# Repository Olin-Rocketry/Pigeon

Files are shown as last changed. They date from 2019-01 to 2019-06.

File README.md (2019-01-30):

# Pigeon
simple flight computer to serve as a learning bed for embedded software and pcb design.

## Features
- atmega328p-AU
- battery connector (JST-PH 2-pin)
- 3-axis accelerometer (ADXL345)
- 2 or 3 programming leds
- SD-Card reader
-level stepper for SD-Card

## Requirements
- fit in our current rocket (same dimensions as peregrine)
- run time greater than 30 minutes

## Goals
- learning platform for incoming members
- test/optimize SD-Card write performance

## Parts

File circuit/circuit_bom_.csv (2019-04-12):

Component | Description | Part | References | Value | Footprint | Quantity Per PCB | Datasheet | MFN | MPN | PurchasingLink | Purchasing Link | Digi-Key Part Number
1 | b'' | b'C_0.1uF' | b'C2' | b'C_0.1uF' | b'C_0805_OEM' | b'1' | b'http://datasheets.avx.com/X7RDielectric.pdf' | b'DK' | b'478-3352-1-ND' | b'https://www.digikey.com/products/en?keywords=478-3352-1-ND' | b'' | b''
2 | b'' | b'C_0.1uF' | b'C7' | b'C_0.1uF' | b'C_0805_OEM' | b'1' | b'http://datasheets.avx.com/X7RDielectric.pdf' | b'DK' | b'478-3352-1-ND' | b'https://www.digikey.com/products/en?keywords=478-3352-1-ND' | b'' | b''
3 | b'' | b'C_0.1uF' | b'C9' | b'C_0.1uF' | b'C_0805_OEM' | b'1' | b'http://datasheets.avx.com/X7RDielectric.pdf' | b'DK' | b'478-3352-1-ND' | b'https://www.digikey.com/products/en?keywords=478-3352-1-ND' | b'' | b''
4 | b'' | b'C_100pF' | b'C6' | b'C_100pF' | b'C_0805_OEM' | b'1' | b'https://katalog.we-online.de/pbs/datasheet/885012007057.pdf' | b'DK' | b'732-7852-1-ND' | b'https://www.digikey.com/product-detail/en/wurth-electronics-inc/885012007057/732-7852-1-ND/5454479' | b'' | b''
5 | b'' | b'C_1uF' | b'C1' | b'C_1uF' | b'C_0805_OEM' | b'1' | b'http://www.samsungsem.com/kr/support/product-search/mlcc/__icsFiles/afieldfile/2018/06/20/CL21A105KAFNNNE.pdf' | b'DK' | b'1276-2887-1-ND' | b'https://www.digikey.com/product-detail/en/samsung-electro-mechanics/CL21A105KAFNNNE/1276-2887-1-ND/3890973' | b'' | b''
6 | b'' | b'C_1uF' | b'C3' | b'C_1uF' | b'C_0805_OEM' | b'1' | b'http://www.samsungsem.com/kr/support/product-search/mlcc/__icsFiles/afieldfile/2018/06/20/CL21A105KAFNNNE.pdf' | b'DK' | b'1276-2887-1-ND' | b'https://www.digikey.com/product-detail/en/samsung-electro-mechanics/CL21A105KAFNNNE/1276-2887-1-ND/3890973' | b'' | b''
7 | b'' | b'C_1uF' | b'C8' | b'C_1uF' | b'C_0805_OEM' | b'1' | b'http://www.samsungsem.com/kr/support/product-search/mlcc/__icsFiles/afieldfile/2018/06/20/CL21A105KAFNNNE.pdf' | b'DK' | b'1276-2887-1-ND' | b'https://www.digikey.com/product-detail/en/samsung-electro-mechanics/CL21A105KAFNNNE/1276-2887-1-ND/3890973' | b'' | b''
8 | b'' | b'C_30pF' | b'C4 C5' | b'C_30pF' | b'C_0805_OEM' | b'2' | b'https://media.digikey.com/pdf/Data%20Sheets/Samsung%20PDFs/CL_Series_MLCC_ds.pdf' | b'DK' | b'1276-1130-1-ND' | b'https://www.digikey.com/product-detail/en/samsung-electro-mechanics-america-inc/CL21C300JBANNNC/1276-1130-1-ND/3889216' | b'' | b''
9 | b'' | b'LED_0805' | b'D1 D2 D3' | b'LED_0805' | b'LED_0805_OEM' | b'3' | b'http://www.osram-os.com/Graphics/XPic9/00078860_0.pdf' | b'DK' | b'475-1410-1-ND' | b'https://www.digikey.com/products/en?keywords=475-1410-1-ND' | b'' | b''
10 | b'' | b'JST-PH_2_RA' | b'J1' | b'JST-PH_2_RA' | b'JST-PH_2_RA' | b'1' | b'https://cdn-shop.adafruit.com/datasheets/17311.pdf' | b'' | b'' | b'' | b'https://www.adafruit.com/product/1769' | b''
11 | b'' | b'R_100' | b'R7' | b'R_100' | b'R_0805_OEM' | b'1' | b'https://www.seielect.com/Catalog/SEI-rncp.pdf' | b'DK' | b'RNCP0805FTD100RCT-ND' | b'https://www.digikey.com/products/en?keywords=RNCP0805FTD100RCT-ND' | b'' | b''
12 | b'' | b'R_10K' | b'R9 R11' | b'R_10K' | b'R_0805_OEM' | b'2' | b'http://www.bourns.com/data/global/pdfs/CRS.pdf' | b'DK' | b'CRS0805-FX-1002ELFCT-ND' | b'https://www.digikey.com/products/en?keywords=CRS0805-FX-1002ELFCT-ND' | b'' | b''
13 | b'' | b'R_10K' | b'R4 R6' | b'R_10K' | b'R_0805_OEM' | b'2' | b'http://www.bourns.com/data/global/pdfs/CRS.pdf' | b'DK' | b'CRS0805-FX-1002ELFCT-ND' | b'https://www.digikey.com/products/en?keywords=CRS0805-FX-1002ELFCT-ND' | b'' | b''
14 | b'' | b'R_200' | b'R1 R2 R3 R5' | b'R_200' | b'R_0805_OEM' | b'4' | b'https://www.seielect.com/Catalog/SEI-RMCF_RMCP.pdf' | b'DK' | b'RMCF0805JT200RCT-ND' | b'https://www.digikey.com/products/en?keywords=RMCF0805JT200RCT-ND' | b'' | b''
15 | b'' | b'R_4.7K' | b'R8 R10' | b'R_4.7K' | b'R_0805_OEM' | b'2' | b'http://www.yageo.com/documents/recent/PYu-RC_Group_51_RoHS_L_8.pdf' | b'DK' | b'311-4.7KARCT-ND' | b'https://www.digikey.com/product-detail/en/yageo/RC0805JR-074K7L/311-4.7KARCT-ND/731274' | b'' | b''
16 | b'' | b'Micro_SD_Card_A118117CT-ND' | b'SD1' | b'Micro_SD_Card_A118117CT-ND' | b'Micro_SD_Card_A118117CT-ND' | b'1' | b'https://www.te.com/commerce/DocumentDelivery/DDEController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' | b'' | b'2201778-1' | b'' | b'' | b'A118117CT-ND'
17 | b'' | b'4050_Logic_Buffer' | b'U6' | b'4050_Logic_Buffer' | b'SOIC-16_3.9x9.9mm_Pitch1.27mm' | b'1' | b'www.ti.com/lit/ds/symlink/cd74hc4049.pdf' | b'' | b'' | b'' | b'https://www.digikey.com/product-detail/en/texas-instruments/CD74HC4050M96/296-14529-1-ND/555596' | b''
18 | b'' | b'ADXL345' | b'U3' | b'ADXL345' | b'ADXL345' | b'1' | b'http://www.analog.com/media/en/technical-documentation/data-sheets/ADXL345.pdf' | b'DK' | b'ADXL345BCCZ-ND' | b'https://www.digikey.com/product-detail/en/analog-devices-inc/ADXL345BCCZ/ADXL345BCCZ-ND/2034829' | b'' | b''
19 | b'20MHz, 32kB Flash, 2kB SRAM, 1kB EEPROM, TQFP-32' | b'ATmega328-AU' | b'U4' | b'ATmega328-AU' | b'TQFP-32_7x7mm_Pitch0.8mm' | b'1' | b'http://ww1.microchip.com/downloads/en/DeviceDoc/ATmega328_P%20AVR%20MCU%20with%20picoPower%20Technology%20Data%20Sheet%2040001984A.pdf' | b'' | b'' | b'' | b'' | b''
20 | b'' | b'SK812' | b'U1' | b'SK812' | b'SK6812' | b'1' | b'https://cdn-shop.adafruit.com/product-files/1138/SK6812+LED+datasheet+.pdf' | b'' | b'' | b'https://www.digikey.com/product-detail/en/adafruit-industries-llc/1655/1528-1104-ND/5154679' | b'' | b''
21 | b'' | b'TCR2EF33LM' | b'U2' | b'TCR2EF33LM' | b'SOT25' | b'1' | b'https://toshiba.semicon-storage.com/info/docget.jsp?did=13794&prodName=TCR2EF45' | b'' | b'TCR2EF33LM(CTCT-ND' | b'' | b'https://www.digikey.com/product-detail/en/toshiba-semiconductor-and-storage/TCR2EF33LM-CT/TCR2EF33LM-CTCT-ND/4503328' | b''
22 | b'' | b'USB_MicroB' | b'U5' | b'USB_MicroB' | b'USB_Micro-B_Molex-105017-0001' | b'1' | b'https://www.molex.com/pdm_docs/sd/1050170001_sd.pdf' | b'DK' | b'WM1399CT-ND' | b'https://www.digikey.com/product-detail/en/molex-llc/1050170001/WM1399CT-ND/2350885' | b'' | b''
23 | b'' | b'Crystal_SMD' | b'Y1' | b'Crystal_SMD' | b'Crystal_SMD_FA238' | b'1' | b'https://support.epson.biz/td/api/doc_check.php?dl=brief_FA-238V_en.pdf' | b'DK' | b'SER3686CT-ND' | b'https://www.digikey.com/products/en?keywords=SER3686CT-ND' | b'' | b''
Component Groups: | 23
Component Count: | 32
Fitted Components: | 32
Number of PCBs: | 1
Total components: | 32
Schematic Version:
Schematic Date:
BoM Date: | b'Tue 02 Apr 2019 08:23:06 PM EDT'
Schematic Source: | b'/home/william/Desktop/pigeon/circuit/circuit.sch'
KiCad Version: | b'Eeschema 5.0.0-fee4fd1~66~ubuntu16.04.1'

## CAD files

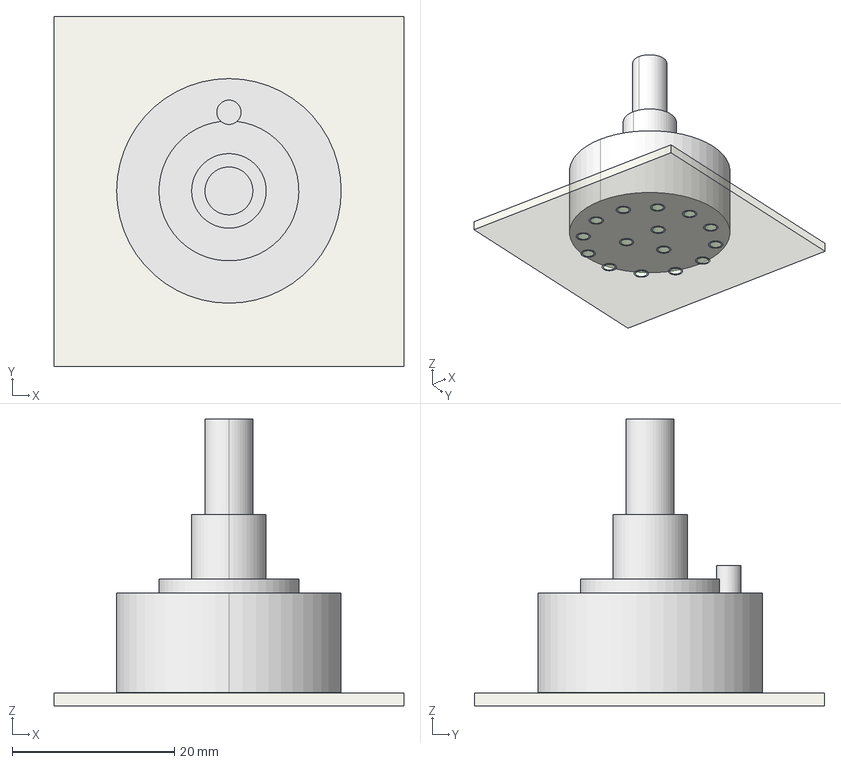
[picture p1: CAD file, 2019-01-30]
3DModels/3P4T_rotary_switch/3P4T_rotary_switch.fcstd
43.2 x 43.2 x 35.4 mm
FrontSilk
TopPads
BotPads
PTHs
Pcb
prog_switch

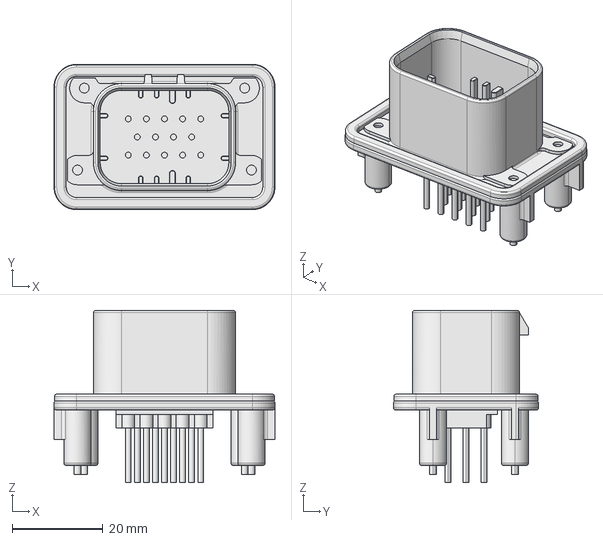
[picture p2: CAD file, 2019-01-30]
3DModels/Ampseal-14/AmpSeal-14.step
48.8 x 32.1 x 38.1 mm

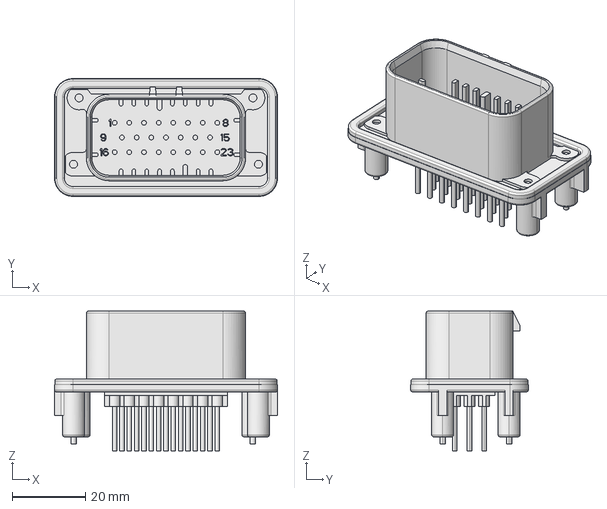
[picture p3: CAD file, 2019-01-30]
3DModels/Ampseal-23/Ampseal_23.step
60.8 x 32.1 x 38.1 mm

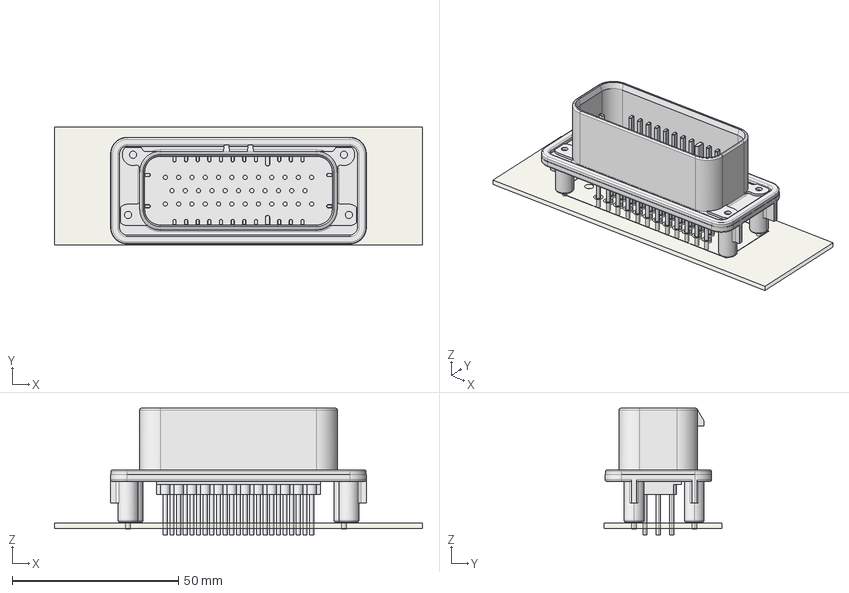
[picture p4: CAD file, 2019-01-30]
3DModels/Ampseal-35/Ampseal-35.fcstd
110.6 x 35.4 x 38.0 mm
FrontSilk
TopPads
BotPads
PTHs
Pcb
C-1-776231-4

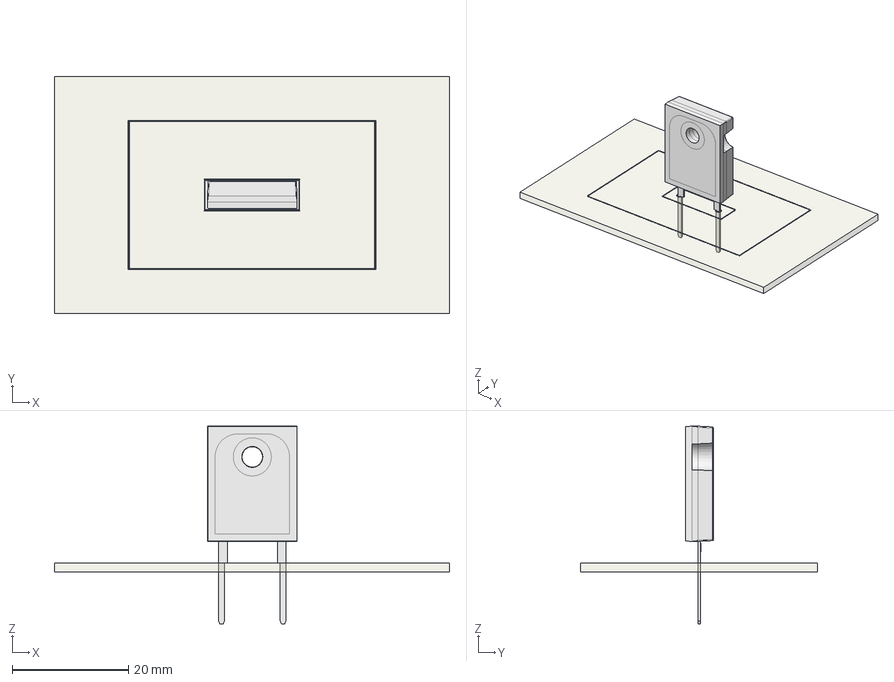
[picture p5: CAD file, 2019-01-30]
3DModels/AP101_3k_resistor/AP101.fcstd
68.0 x 40.8 x 34.0 mm
F_CrtYd
FrontSilk
TopPads
BotPads
PTHs
Pcb
TIP 144_sp

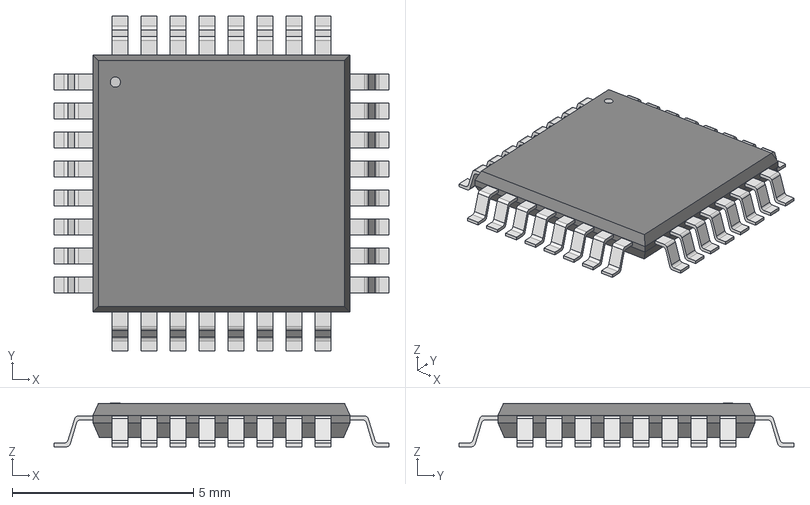
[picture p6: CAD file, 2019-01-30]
3DModels/Atmega16m1/32A-M.step
9.25 x 9.25 x 1.20 mm

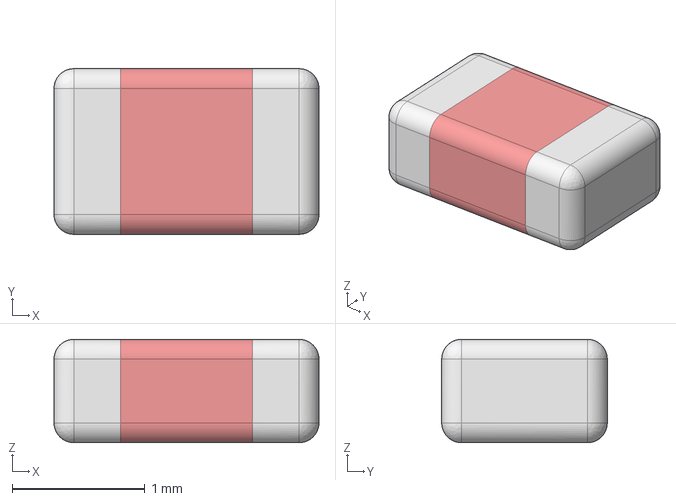
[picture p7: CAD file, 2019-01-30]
3DModels/C_0805_OEM/C_0805.step
2.00 x 1.25 x 0.78 mm

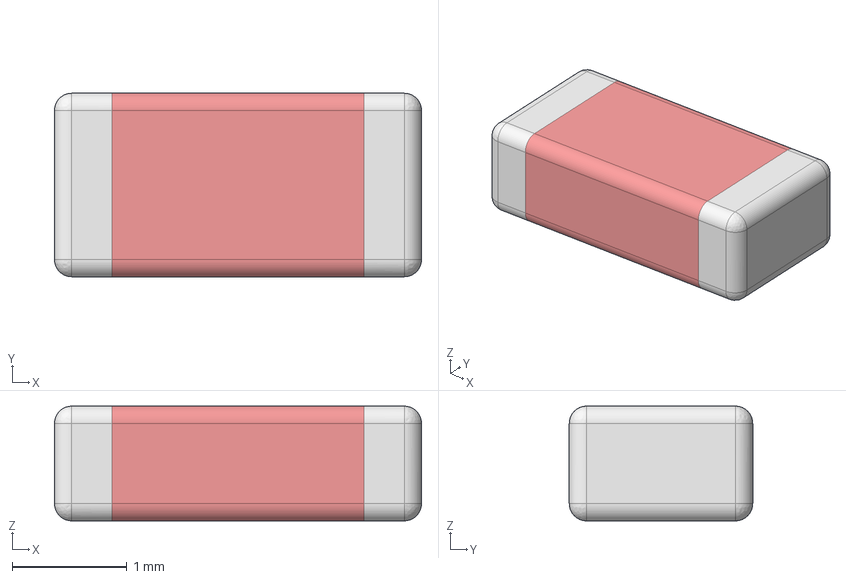
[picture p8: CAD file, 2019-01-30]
3DModels/C_1206_OEM/C_1206_OEM.step
3.20 x 1.60 x 1.00 mm

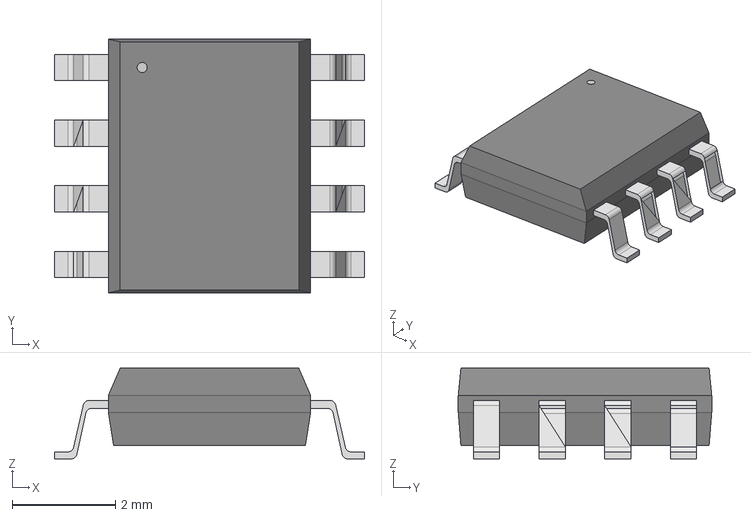
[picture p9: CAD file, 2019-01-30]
3DModels/CAN Transceiver/CAN Transceiver.step
5.99 x 4.90 x 1.75 mm

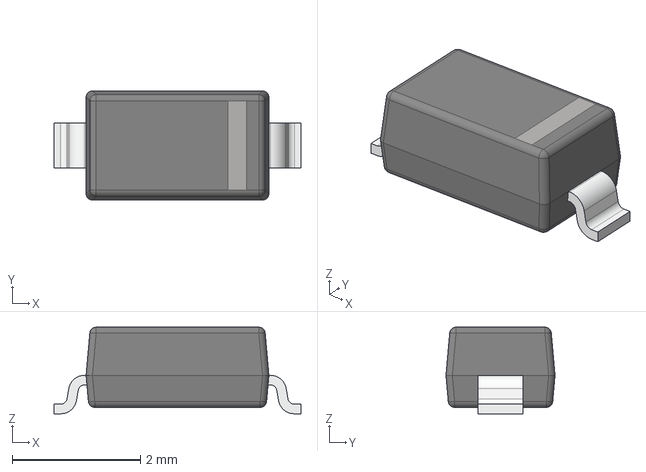
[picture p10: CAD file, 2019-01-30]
3DModels/D_Schottky_SOD123/DO-215AD002_sp.step
3.85 x 1.70 x 1.35 mm

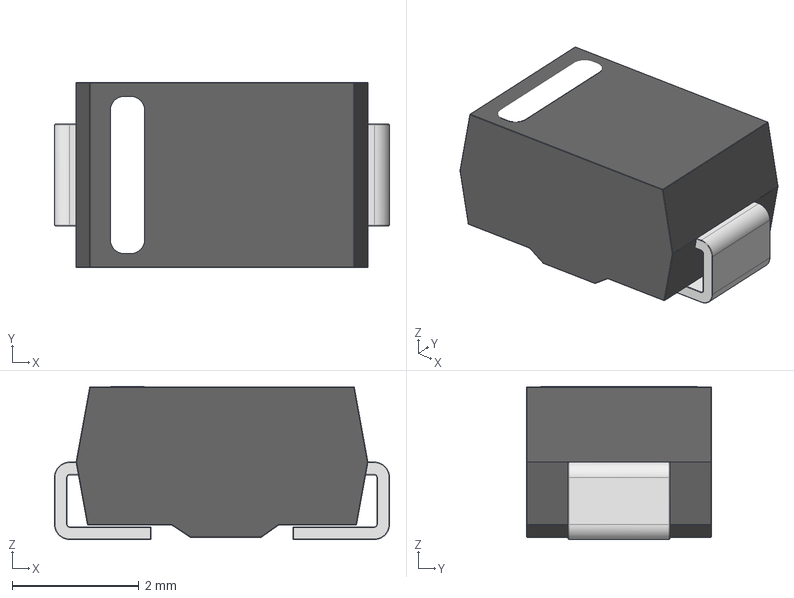
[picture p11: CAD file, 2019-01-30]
3DModels/DO_214AA_OEM/DO_214AA.step
5.28 x 2.92 x 2.41 mm

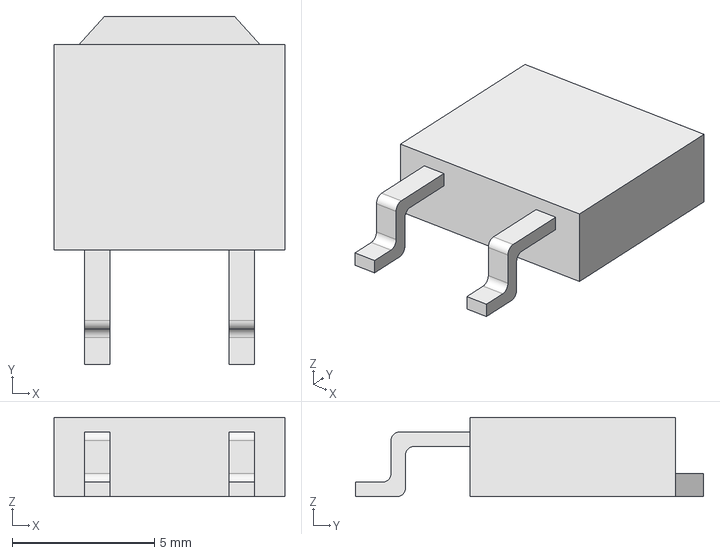
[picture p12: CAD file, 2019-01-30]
3DModels/DTO25/DTO025.step
8.13 x 12.2 x 2.79 mm

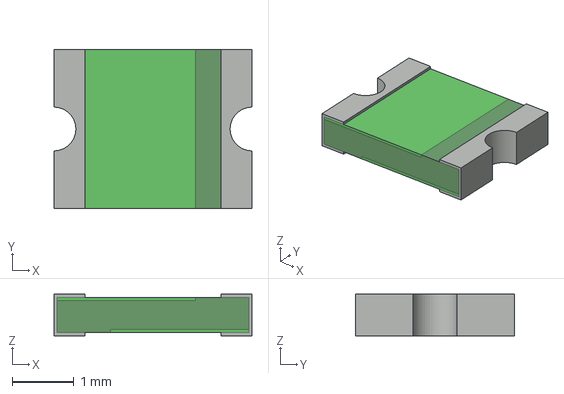
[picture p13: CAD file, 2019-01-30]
3DModels/Fuse_1210_OEM/Fuse1210.step
3.21 x 2.58 x 0.675 mm

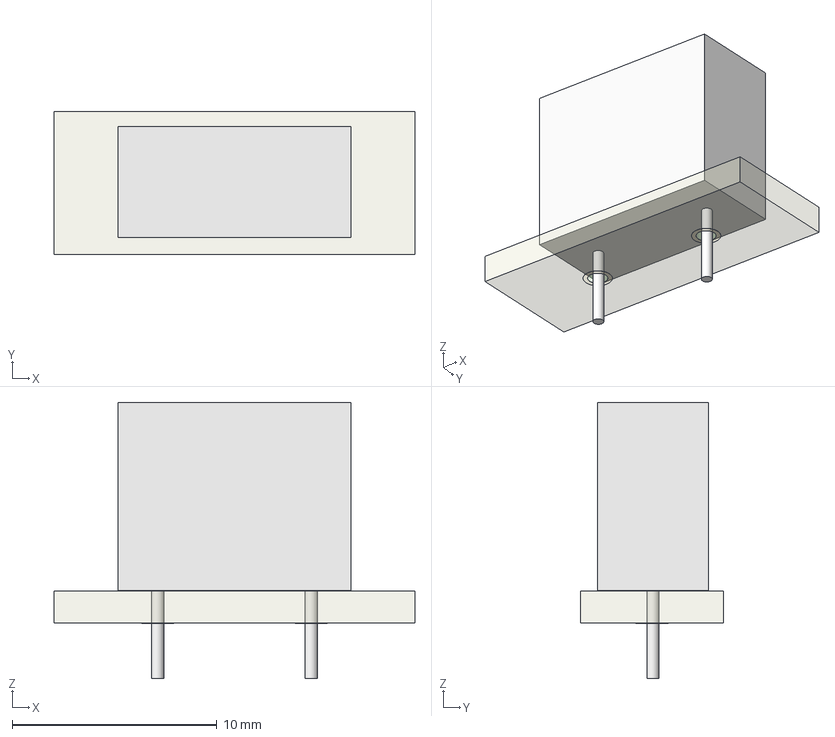
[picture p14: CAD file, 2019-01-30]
3DModels/Fuse_807/Fuse_807.fcstd
17.6 x 6.98 x 13.5 mm
F_CrtYd
FrontSilk
TopPads
BotPads
PTHs
Pcb

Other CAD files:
3DModels/fuse_block/fuse_block.step
3DModels/G5Q_OEM/G5Q.step
3DModels/Header_Pin_2x3/Header_Pin_2x3.fcstd
3DModels/LED_0805/LED_0805.fcstd
3DModels/3352E.stp
3DModels/3P4T_rotary_switch/prog_switch.step
3DModels/AP101_3k_resistor/TIP 144_sp.step
3DModels/Ampseal-14/Ampseal-14.fcstd
3DModels/Ampseal-23/Ampseal-23.fcstd
3DModels/Ampseal-35/C-1-776231-4.step
3DModels/Atmega16m1/Atmega16m1.fcstd
3DModels/Atmega16m1/Atmega16m1.step
3DModels/CAN Transceiver/CAN_Transceiver.fcstd
3DModels/CAN Transceiver/SOIC8-N_MC.step
3DModels/C_0805_OEM/C_0805.fcstd
3DModels/C_1206_OEM/C_1206_OEM.fcstd
3DModels/DO_214AA_OEM/DO_214AA.fcstd
3DModels/DTO25/DTO25.fcstd
3DModels/D_Schottky_SOD123/D_Schottky_SOD123.fcstd
3DModels/Fuse_1210_OEM/Fuse_1210.fcstd
3DModels/Fuse_807/Part 1.step
3DModels/G5Q_OEM/G5Q.fcstd
3DModels/Header_Pin_2x3/Header_Straight_2x3.step
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

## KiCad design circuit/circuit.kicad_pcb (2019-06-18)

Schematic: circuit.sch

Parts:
C1, C8: C_1uF; C_0805_OEM; MPN 1276-2887-1-ND
C2, C3: C_10uF; C_0805_OEM; MPN 1276-1052-1-ND
C4, C5: C_30pF; C_0805_OEM; MPN 1276-1130-1-ND
C6: C_100pF; C_0805_OEM; MPN 732-7852-1-ND
C7, C9: C_0.1uF; C_0805_OEM; MPN 478-3352-1-ND
D1, D2, D3: LED_0805; LED_0805_OEM; MPN 475-1410-1-ND
J1: JST-PH_2_RA
J2: CONN_02X03; Pin_Header_Straight_2x03; MPN 609-3234-ND
R1, R2, R3, R5: R_200; R_0805_OEM; MPN RMCF0805JT200RCT-ND
R4, R6, R8, R9, R11: R_10K; R_0805_OEM; MPN CRS0805-FX-1002ELFCT-ND
R7: R_100; R_0805_OEM; MPN RNCP0805FTD100RCT-ND
SD1: MicroSD_V2; Micro_SD_Card_Holder_Molex; MPN 0473521001; Digi-Key Part Number WM3290CT-ND
U1: SK812; SK6812
U2: LM1117MPX-3.3; SOT-223
U3: ADXL345; MPN ADXL345BCCZ-ND
U4: ATmega328-AU; TQFP-32_7x7mm_Pitch0.8mm
Y1: Crystal_SMD; Crystal_SMD_FA238; MPN SER3686CT-ND

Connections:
/Battery+: C2.1, J1.1, U2.3
/Dectect_LED: R2.1, SD1.9, U4.12 (PB0)
/INT1: U3.8, U4.14 (PB2)
/INT2: U3.9, U4.13 (PB1)
/MISO: J2.1, SD1.7, U4.16 (PB4)
/MOSI: J2.4, SD1.3, U4.15 (PB3)
/Neopix: R5.2, U4.26 (PC3)
/P_LED_1: D2.2, U4.24 (PC1)
/RESET: J2.5, R6.1, U4.29 (~RESET~/PC6)
/SCK: J2.3, SD1.5, U4.17 (PB5)
/SCL: R4.2, U3.14, U4.28 (PC5)
/SDA: R8.2, U3.13, U4.27 (PC4)
/SD_CS: SD1.2, U4.11 (PD7)
GND: C1.2, C2.2, C3.2, C4.2, C5.2, C6.2, C7.1, C8.2, C9.2, D1.1, J1.2, J2.6, R1.1, R3.1, R11.2, SD1.6, U1.1, U2.1, U3.2, U3.4, U3.5, U4.3 (GND), U4.5 (GND), U4.21 (GND), Y1.2, Y1.4
unnamed: C4.1, U4.7 (XTAL1/PB6), Y1.1
unnamed: C5.1, U4.8 (XTAL2/PB7), Y1.3
unnamed: C6.1, R7.2, U4.18 (AVCC)
unnamed: D1.2, R2.2
unnamed: D2.1, R1.2
unnamed: D3.1, R3.2
unnamed: R5.1, U1.2
unnamed: R9.2, U3.7
unnamed: R11.1, U3.12
VCC: C1.1, C3.1, C7.2, C8.1, C9.1, D3.2, J2.2, R4.1, R6.2, R7.1, R8.1, R9.1, SD1.4, U1.3, U2.2, U2.4, U3.1, U3.6, U4.4 (VCC), U4.6 (VCC)

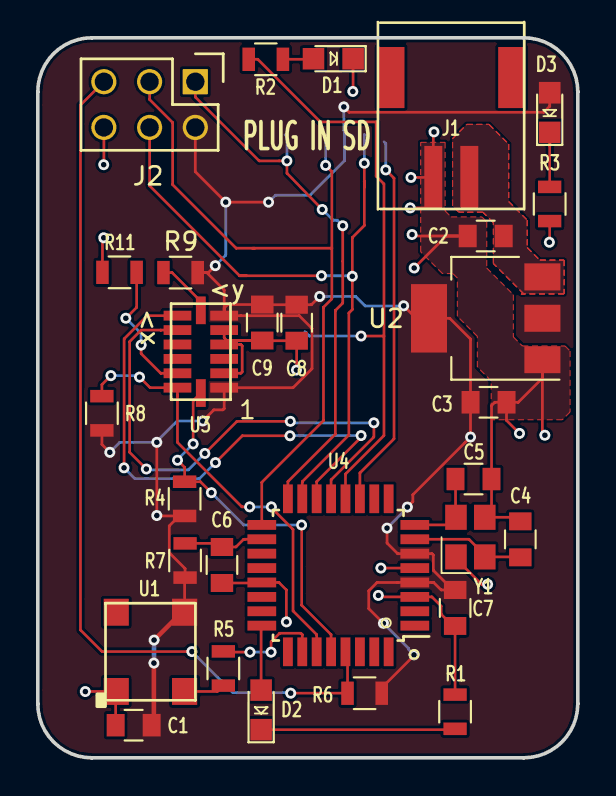
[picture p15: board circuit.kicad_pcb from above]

Board: 2 copper layers, 30.0 x 40.0 mm, 30 parts (1 on the bottom side), 24 nets.

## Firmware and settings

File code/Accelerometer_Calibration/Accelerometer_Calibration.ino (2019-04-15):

#include <Wire.h>
#include <Adafruit_Sensor.h>
#include <Adafruit_ADXL345_U.h>
 
/* Assign a unique ID to this sensor at the same time */
Adafruit_ADXL345_Unified accel = Adafruit_ADXL345_Unified(12345);
 
 
float AccelMinX = 0;
float AccelMaxX = 0;
float AccelMinY = 0;
float AccelMaxY = 0;
float AccelMinZ = 0;
float AccelMaxZ = 0;
 
 
void setup(void) 
{
  Serial.begin(9600);
  Serial.println("ADXL345 Accelerometer Calibration"); 
  Serial.println("");
  
  /* Initialise the sensor */
  if(!accel.begin())
  {
    /* There was a problem detecting the ADXL345 ... check your connections */
    Serial.println("Ooops, no ADXL345 detected ... Check your wiring!");
    while(1);
  }
}
 
void loop(void)
{
    Serial.println("Type key when ready..."); 
    while (!Serial.available()){}  // wait for a character
    
    /* Get a new sensor event */ 
    sensors_event_t accelEvent;  
    accel.getEvent(&accelEvent);
    
    if (accelEvent.acceleration.x < AccelMinX) AccelMinX = accelEvent.acceleration.x;
    if (accelEvent.acceleration.x > AccelMaxX) AccelMaxX = accelEvent.acceleration.x;
    
    if (accelEvent.acceleration.y < AccelMinY) AccelMinY = accelEvent.acceleration.y;
    if (accelEvent.acceleration.y > AccelMaxY) AccelMaxY = accelEvent.acceleration.y;
  
    if (accelEvent.acceleration.z < AccelMinZ) AccelMinZ = accelEvent.acceleration.z;
    if (accelEvent.acceleration.z > AccelMaxZ) AccelMaxZ = accelEvent.acceleration.z;
  
    Serial.print("Accel Minimums: "); Serial.print(AccelMinX); Serial.print("  ");Serial.print(AccelMinY); Serial.print("  "); Serial.print(AccelMinZ); Serial.println();
    Serial.print("Accel Maximums: "); Serial.print(AccelMaxX); Serial.print("  ");Serial.print(AccelMaxY); Serial.print("  "); Serial.print(AccelMaxZ); Serial.println();
 
    while (Serial.available())
    {
      Serial.read();  // clear the input buffer
    }
}

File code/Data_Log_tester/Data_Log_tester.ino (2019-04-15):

// SD libs
#include <SD.h>
#include <SPI.h>

// accel libs
#include <Wire.h>
#include <Adafruit_Sensor.h>
#include <Adafruit_ADXL345_U.h>
Adafruit_ADXL345_Unified accel = Adafruit_ADXL345_Unified(12345); 
 

// var for SD
File myFile;
File myData;
int pinCS = 10; // Pin 10 on Arduino Uno

void setup() {

  // Power
  pinMode(2, OUTPUT);
  digitalWrite(2,HIGH);

  
  Serial.begin(9600);
  pinMode(pinCS, OUTPUT);
  
  // SD Card Initialization and aceel 
  if (SD.begin())
  {
    Serial.println("SD card is ready to use.");
  } else
  {
    Serial.println("SD card initialization failed");
    return;
  }
  if(!accel.begin())
  {
    /* There was a problem detecting the ADXL345 ... check your connections */
    Serial.println("Ooops, no ADXL345 detected ... Check your wiring!");
    while(1);
  }

  
  // Create/Open file 
  myFile = SD.open("test.txt", FILE_WRITE);
  
  // if the file opened okay, write to it:
  if (myFile) {
    Serial.println("Writing to file...");
    // Write to file
    myFile.println("Testing text 1, 2 ,3...");
    myFile.close(); // close the file
    Serial.println("Done.");
  }
  // if the file didn't open, print an error:
  else {
    Serial.println("error opening test.txt");
  }
  // Reading the file
  myFile = SD.open("test.txt");
  if (myFile) {
    Serial.println("Read:");
    // Reading the whole file
    while (myFile.available()) {
      Serial.write(myFile.read());
   }
    myFile.close();
  }
  else {
    Serial.println("error opening test.txt");
  }

  delay(1000);
  Serial.println("starting to take data");
  myData = SD.open("data.txt", FILE_WRITE); 
  for(int i = 0; i < 1000; i++){
    sensors_event_t accelEvent;  
    accel.getEvent(&accelEvent);
    myData.print("X: ");
    myData.print(accelEvent.acceleration.x);
    myData.print("Y: ");
    myData.println(accelEvent.acceleration.y);
//    Serial.print("X: ");
//    Serial.print(accelEvent.acceleration.x);
//    Serial.print(" Y: ");
//    Serial.println(accelEvent.acceleration.y);
    }
  myData.close(); 
  Serial.println("Done taking data"); 
  
}
void loop() {
  // empty
}

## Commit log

2019-01-30 added library
    [1722861104.step, 1723101302.step, 194270032.step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]
2019-01-30 First draft of the circuit schematic
    [circuit.kicad_pcb, circuit.sch]
2019-02-02 Pushing the changes to the schematic
    [circuit.sch]
2019-02-02 Pushing the new schematic
2019-02-06 updated schematic
    [circuit.sch]
2019-02-08 Version one of the schematic with footprints
    [circuit.sch]
2019-02-08 Pushing the footprint
2019-02-09 schematic edited
    [circuit.sch]
2019-02-13 Pushing the edited symbols and footprints
2019-02-13 We can final make the layout
    [circuit.sch]
2019-02-15 oh geez. windows and ubuntu
    [circuit.sch]
2019-02-17 modified schematic and layout:
    [circuit.kicad_pcb, circuit.sch]
2019-02-17 did some more work on the layout. added some graphics
    [circuit.kicad_pcb]
2019-04-12 revision two
    [circuit-B.Cu.gbr, circuit-B.Mask.gbr, circuit-B.Paste.gbr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]
2019-04-12 starting rev 3
    [circuit.kicad_pcb, circuit.sch]
2019-04-12 Footprint for the Molex Micro sd card holder
2019-04-15 updated new microsd footprint
2019-04-17 working on rev3
    [circuit.kicad_pcb, circuit.sch]
2019-04-17 Did some more vias and traces - I don't know if this board looks good
    [circuit.kicad_pcb]
2019-04-17 Did some moving around of parts and made the layout cleaner. I think this looks better!
    [circuit.kicad_pcb]
2019-04-24 Latest updates to the PCB design
    [circuit.kicad_pcb]
2019-05-01 Final REV4 Board
2019-05-21 Layout with a 2x03 connector
    [circuit.kicad_pcb]
2019-05-21 Schematic with a 2x03 connector
    [circuit.sch]
2019-05-22 Fixed the text labels and revision number.
    [circuit.kicad_pcb]
2019-05-23 Added the pigeon mark on the back
    [circuit.kicad_pcb]
